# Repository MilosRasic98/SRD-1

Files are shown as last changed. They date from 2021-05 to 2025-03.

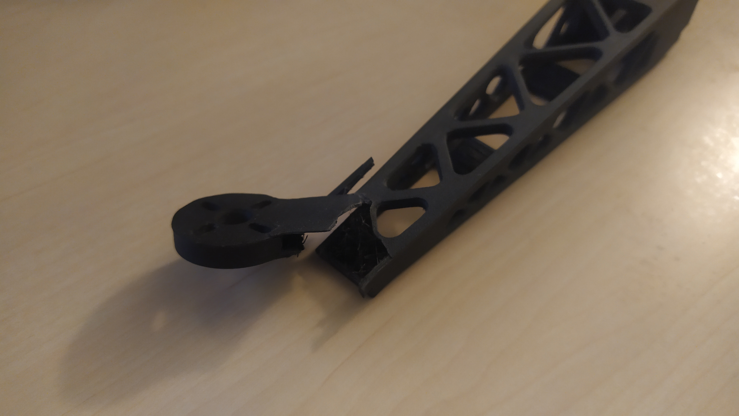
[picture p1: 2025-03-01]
Pictures/1621984355056.jpg

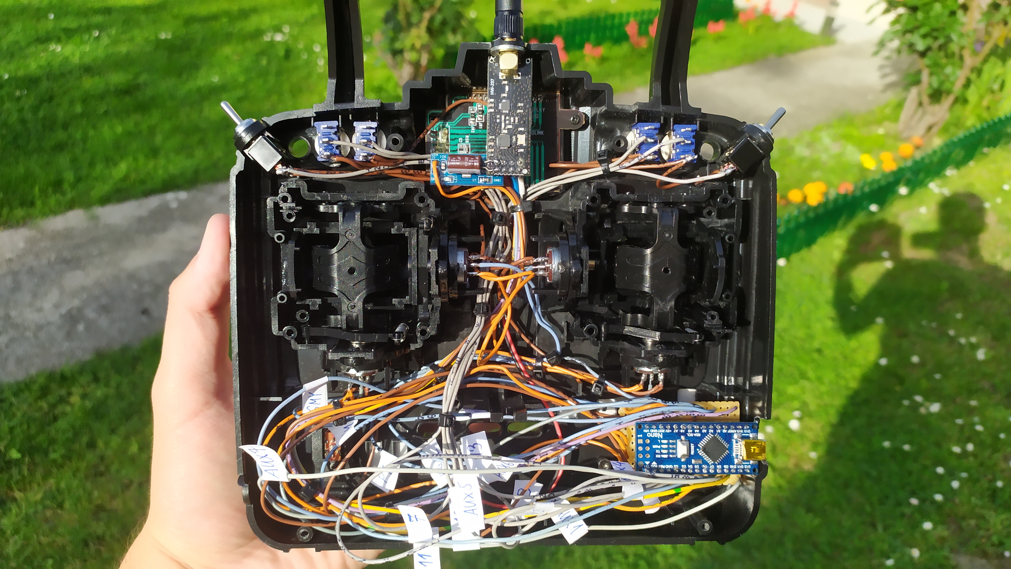
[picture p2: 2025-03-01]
Pictures/1621959381772.jpg

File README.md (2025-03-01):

# DIY Arduino Drone SRD-1

This repository covers the development of a completely open-source drone that I named the SRD-1. SRD-1 stands for Science & Research Drone 1 (the name was of course inspired by the legendary plane SR-71 Blackbird). For motors and ESCs, this drone uses the generic 2212 motors with the generic 30A ESC-s, meaning that those parts can be easily acquired by anyone. As for the rest of the electronics, all 3 major systems of the drone are based on individual Arduino Nanos. This includes:

1. Flight Controller - Arduino Nano, paired with an MPU6050, running the open-source MultiWii firmware
2. Radio Receiver - Arduino Nano, paired with the RF NRF module, code available in this repository
3. Radio Transmitter - Arduino Nano, paired with the RF NRF module, code available in this repository

If you check out the folders, you'll also be able to find all of the necessary CAD files for building your own drone. I will also be posting all of these models on Printables so you can download them there more easily if you would like. Links to Printables models:

1. https://www.printables.com/model/1212696-diy-arduino-drone-srd-1
2. https://www.printables.com/model/227060-raspberry-pi-hq-camera-drone-gimbal

I made this drone in 2021 as part of Element14 Communities, Attack of the Drones Project14 Competition, which this project managed to win! If you're interested in my write-up from back then, you can check this link here: https://community.element14.com/challenges-projects/project14/attackofthedrones/b/blog/posts/srd-1---3d-printed-drone-arduino-raspberry---june-11th-update---it-flies

Below, you can find some pictures of the finished drone, flight videos, and crash videos, of course!











My goal with this drone was to make it capable, but at the same time, make it as cheap as possible. This is why for the construction of the drone, I went with mostly 3D printed parts, as well as some easily obtainable hardware like PVC pipes so that anyone trying to replicate the drone can have the easiest time possible! Here are some flight videos of the drone, some successful, some a bit less successful, as you can see! Hope you like my sophisticated safety mechanism!

Flight 1

IMAGE ALT TEXT HERE (https://www.youtube.com/watch?v=f9ZAgGi6Brw)

Flight 2

IMAGE ALT TEXT HERE (https://www.youtube.com/watch?v=CNurr2BLMr8)

Flight 3

IMAGE ALT TEXT HERE (https://www.youtube.com/watch?v=EGkVoUZHSek)

Flight 4

IMAGE ALT TEXT HERE (https://www.youtube.com/watch?v=9p4l3mPER5Y)

Drone Crash

IMAGE ALT TEXT HERE (https://www.youtube.com/watch?v=lXBSGYBcmdE)

If you're considering making a similar drone and are curious about the lift capabilities, before making this drone, I made a drone motor test stand to find out what kind of thrust I was working with (you can check out the thrust stand, which is also an open-source project here: https://github.com/MilosRasic98/BLDC-Thrust-Tester), each motor could produce 870g of thrust. To get good performance out of the drone, ideally, you would like to keep it below 1.75kg, which is around half the weight of the maximum thrust with all 4 motors at full throttle.



My ultimate goal was to equip this drone with a Raspberry Pi and a Raspberry Pi Camera so I could do some recording and some more advanced stuff, but I never got around to the software part of it. However, I have done CAD models and printed out a gimbal for the Raspberry Pi HQ Camera module as well as some drone mounts for the Raspberry Pi 4. You can find the CAD files for each of these in the 3D Model directories or on the Printables links that I've linked at the beginning of this Readme file.





As mentioned above, both the RC transmitter and receiver were also made using Arduino Nano boards. To make my life a bit easier when I was making this drone, I used an RC transmitter body from an old RC helicopter I had and just connected it by soldering wires to the potentiometers. Another way you can go to recreate this would be using something like the Arduino joystick modules and keeping the code essentially the same.







I've tried my hardest to design all of the mechanical parts with the manufacturing process in mind, in this case, 3D printing. This is why I tried my best to minimize the support material used, as well as optimize the printability of the parts so that the parts can get the most strength where they need it. I've left a lot of comments in the technical drawings section, which you can check below, or check all of it in the technical drawings directory!





















These are the same principles I tried to keep when I designed the gimbal for the Raspberry Pi HQ Camera using the popular SG90 servo motors. Here, I used some pieces of rubber tubing to act as shock absorbers to at least try and remove some of the noise coming from the propellers while the drone is flying.



















Hope you like the project and that it at least inspires you to make something similar. Feel free to write to me if you have any questions with the project itself!

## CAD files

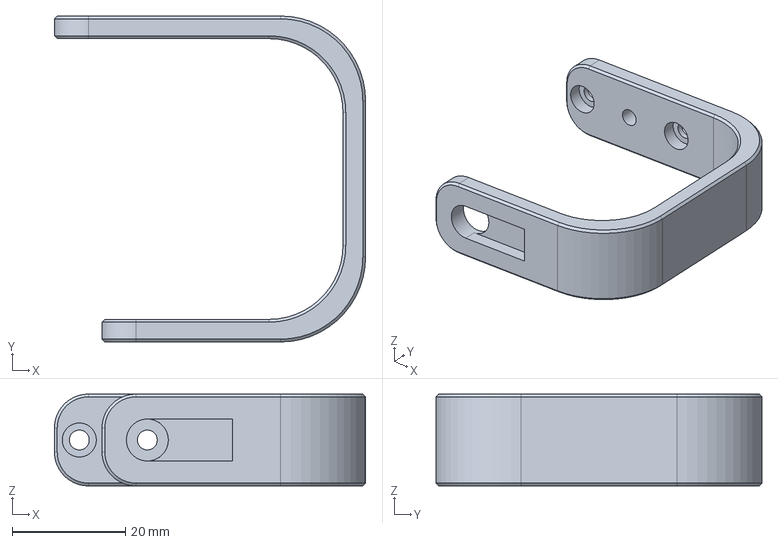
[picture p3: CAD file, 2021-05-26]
3D Models/SG90 Gimbal Assembly/Gimbal Main Arm.step
54.9 x 57.5 x 16.2 mm

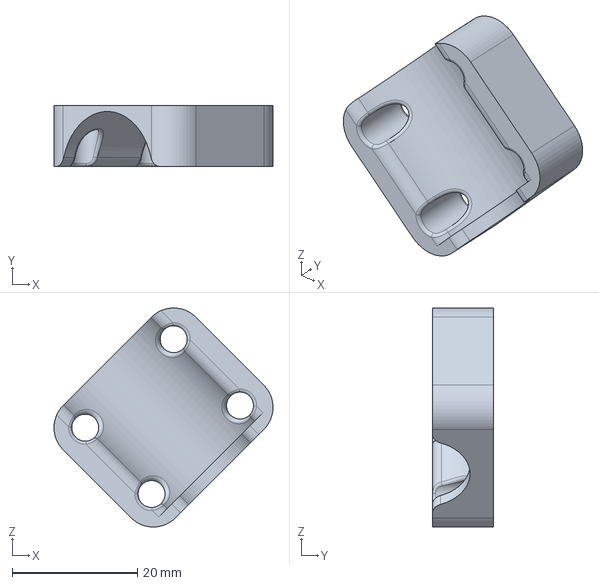
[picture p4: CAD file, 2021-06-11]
3D Models for the 20mm pipe version/Base Assembly/Pipe Arm Mount Half.step
35.0 x 9.75 x 35.0 mm

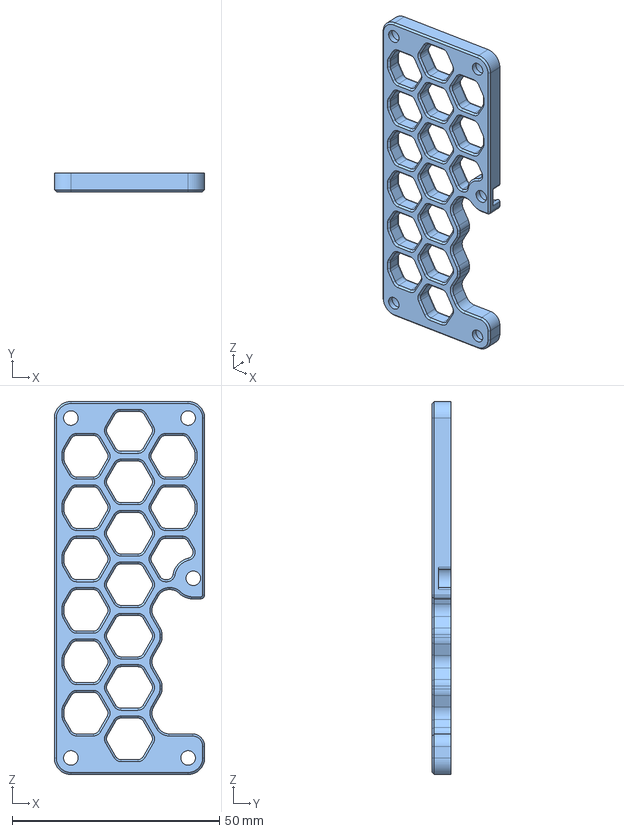
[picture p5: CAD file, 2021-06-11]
3D Models for the 20mm pipe version/Controller Assembly/Electronics Cover.step
36.3 x 4.50 x 90.0 mm

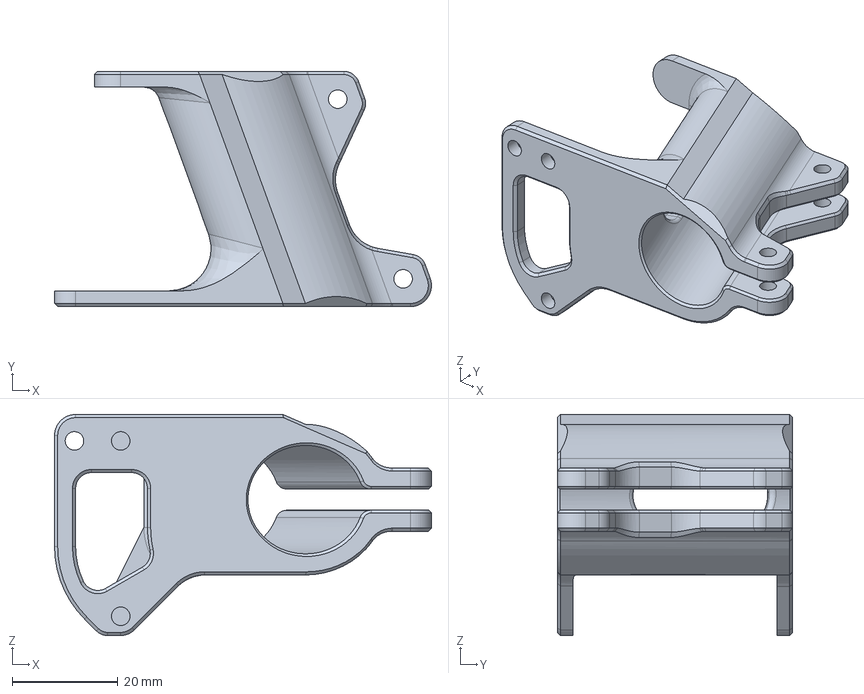
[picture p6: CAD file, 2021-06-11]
3D Models for the 20mm pipe version/Leg Assembly/Leg Holder.step
71.3 x 44.5 x 41.8 mm

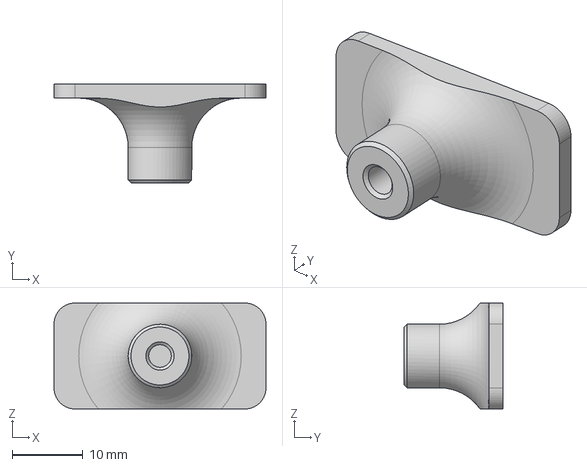
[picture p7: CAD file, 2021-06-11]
3D Models for the 20mm pipe version/Motor Alignment Tool/LevelMount.step
30.0 x 14.0 x 15.0 mm

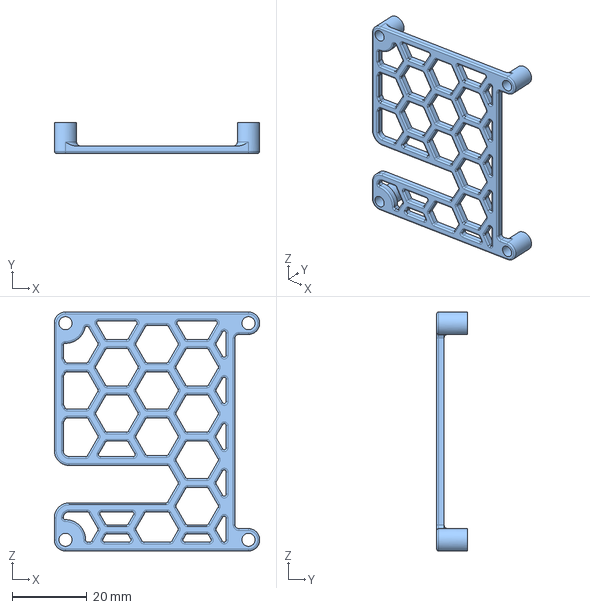
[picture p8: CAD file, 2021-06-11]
3D Models for the 20mm pipe version/Raspberry Pi Assembly/Raspberry Pi Cover.step
55.0 x 8.20 x 64.0 mm

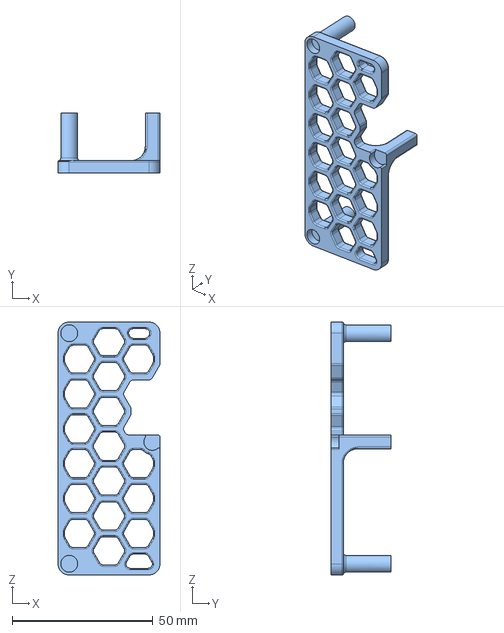
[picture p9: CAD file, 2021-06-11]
3D Models for the 20mm pipe version/Receiver Assembly/Receiver Cover.step
36.3 x 21.5 x 90.0 mm

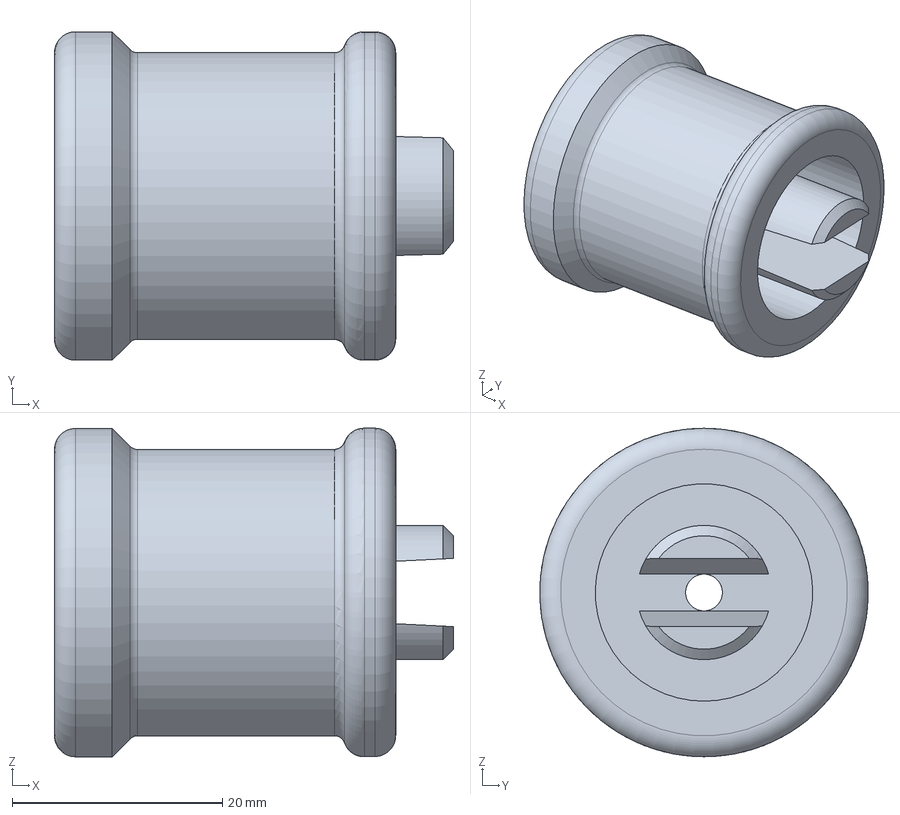
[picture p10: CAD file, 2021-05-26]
3D Models/Base Assembly/Foot.step
38.0 x 31.3 x 31.3 mm

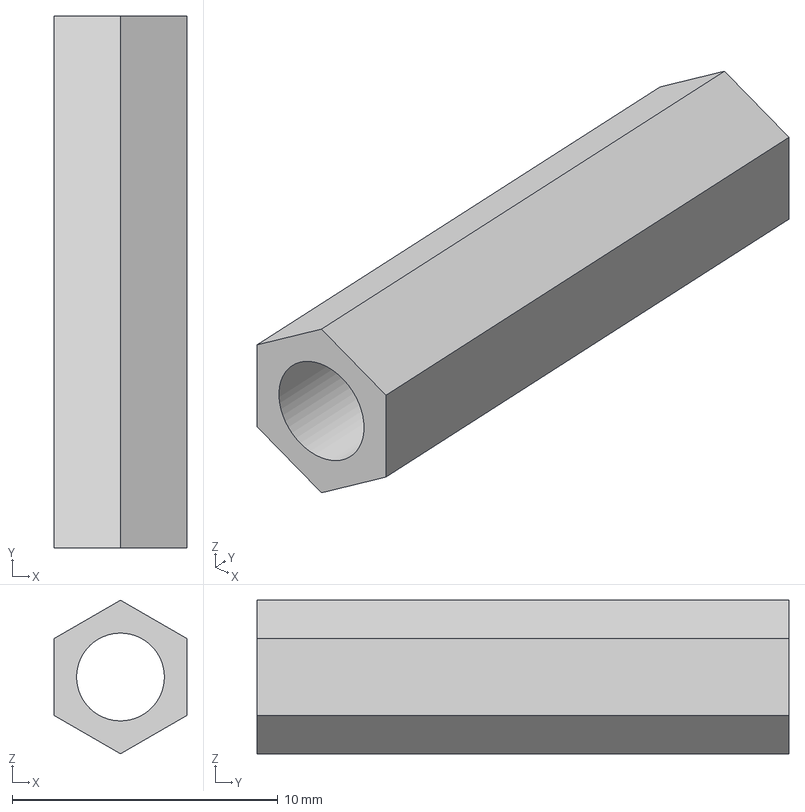
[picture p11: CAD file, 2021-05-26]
3D Models/Electronics Assembly/StandOff.step
5.00 x 20.0 x 5.77 mm

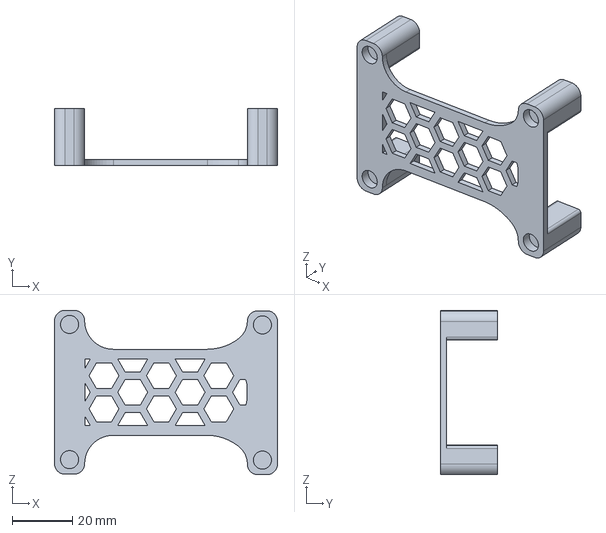
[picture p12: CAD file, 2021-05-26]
3D Models/Power Assembly/Cover.step
74.0 x 19.0 x 54.6 mm

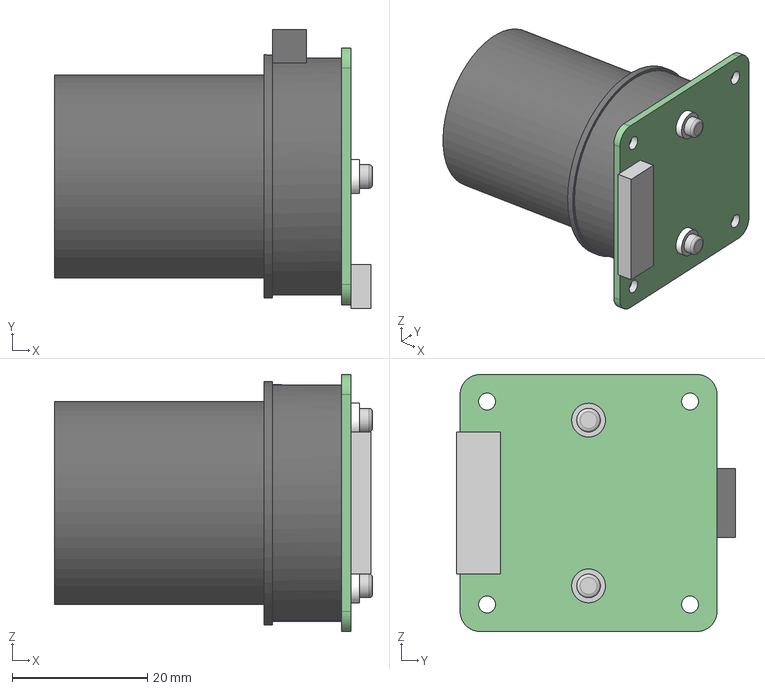
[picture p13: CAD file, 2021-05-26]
3D Models/SG90 Gimbal Assembly/Raspberry HQ Camera.step
47.0 x 41.2 x 38.0 mm

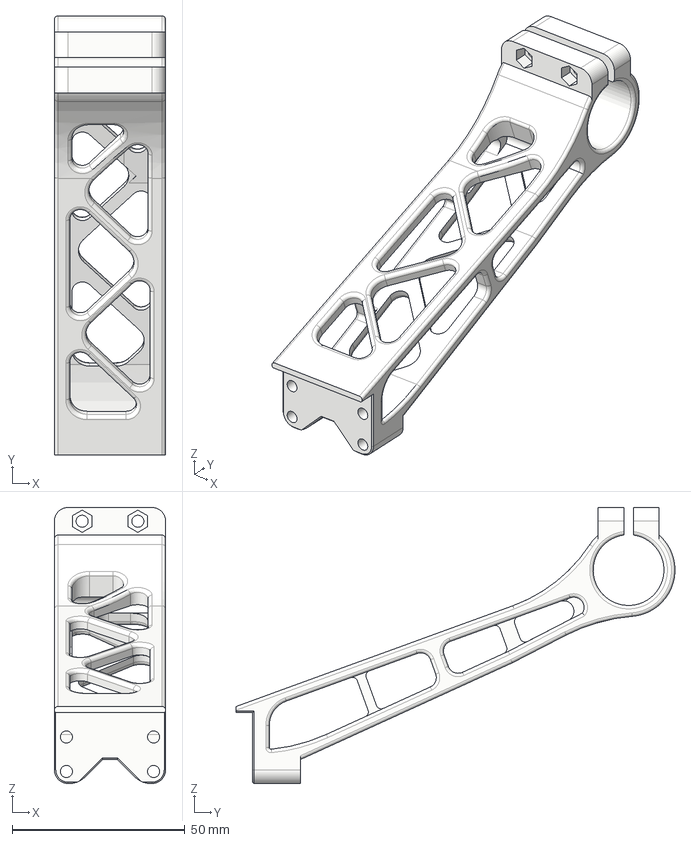
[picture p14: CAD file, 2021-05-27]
3D Models/Wooden Base Version/Left Leg.step
32.3 x 127.2 x 80.0 mm

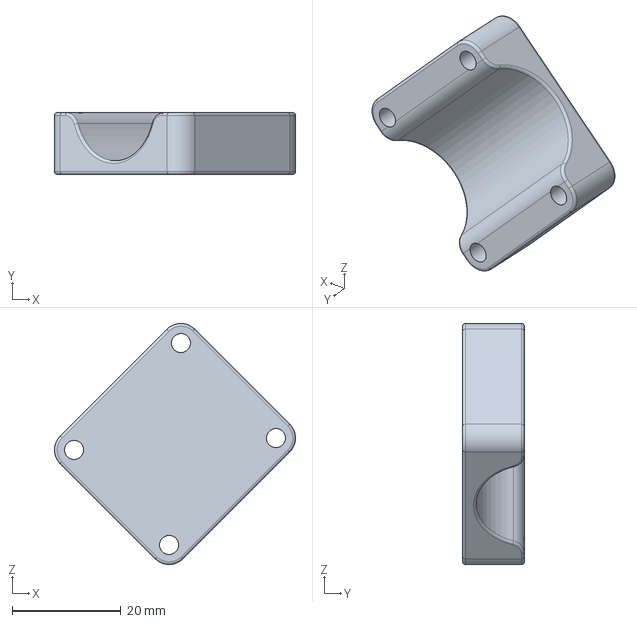
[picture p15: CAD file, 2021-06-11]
3D Models for the 20mm pipe version/Base Assembly/Motor Mount.step
44.3 x 11.4 x 44.3 mm

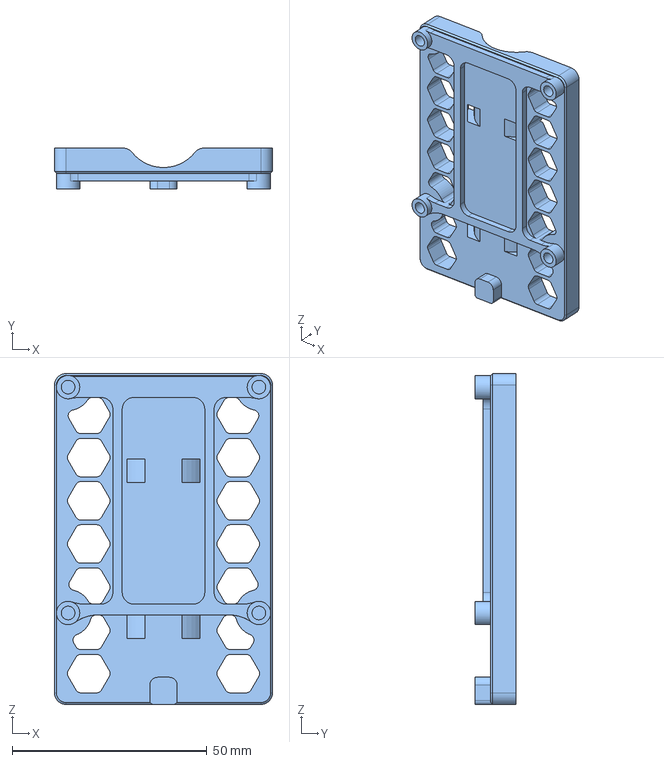
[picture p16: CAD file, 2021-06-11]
3D Models for the 20mm pipe version/Raspberry Pi Assembly/Raspberry Pi Mount.step
56.0 x 10.5 x 85.0 mm

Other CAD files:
3D Models for the 20mm pipe version/Receiver Assembly/Receiver Mount.step
3D Models/Base Assembly/Drone Arm.step
3D Models/Electronics Assembly/Board.step
3D Models/Power Assembly/3S LiPo .step
3D Models for the 20mm pipe version/Base Assembly/Motor Mount.stl
3D Models for the 20mm pipe version/Base Assembly/Motor Plate.step
3D Models for the 20mm pipe version/Base Assembly/Motor Plate.stl
3D Models for the 20mm pipe version/Base Assembly/Pipe Arm Mount Half.stl
3D Models for the 20mm pipe version/Controller Assembly/Electronics Cover.stl
3D Models for the 20mm pipe version/Leg Assembly/Leg Cover.step
3D Models for the 20mm pipe version/Leg Assembly/Leg Cover.stl
3D Models for the 20mm pipe version/Leg Assembly/Leg Holder.stl
3D Models for the 20mm pipe version/Leg Assembly/Leg Locker.step
3D Models for the 20mm pipe version/Leg Assembly/Leg Locker.stl
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

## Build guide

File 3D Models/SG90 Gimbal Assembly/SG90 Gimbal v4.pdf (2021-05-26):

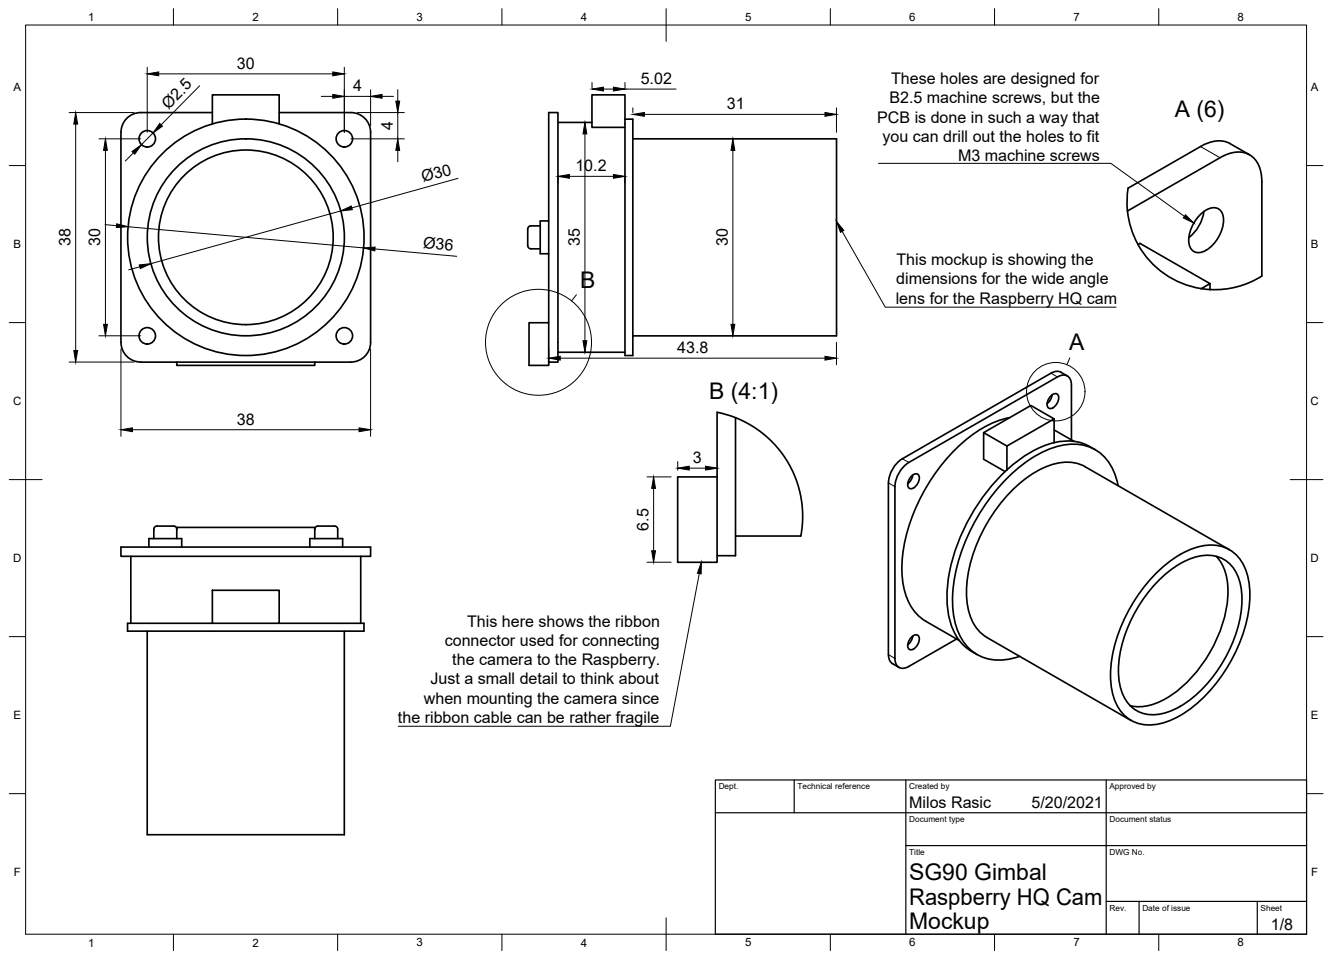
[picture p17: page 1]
Title; DWG No.; Rev.; Date of issue; Sheet; M3 machine screws

These holes are designed for
B2.5 machine screws, but the
PCB is done in such a way that
you can drill out the holes to fit

This mockup is showing the
dimensions for the wide angle
lens for the Raspberry HQ cam

This here shows the ribbon
connector used for connecting
the camera to the Raspberry.
Just a small detail to think about
when mounting the camera since
the ribbon cable can be rather fragile

Dept. | Technical reference | Created by Milos Rasic 5/20/2021 | Approved by

Document type | Document status

SG90 Gimbal
Raspberry HQ Cam
Mockup

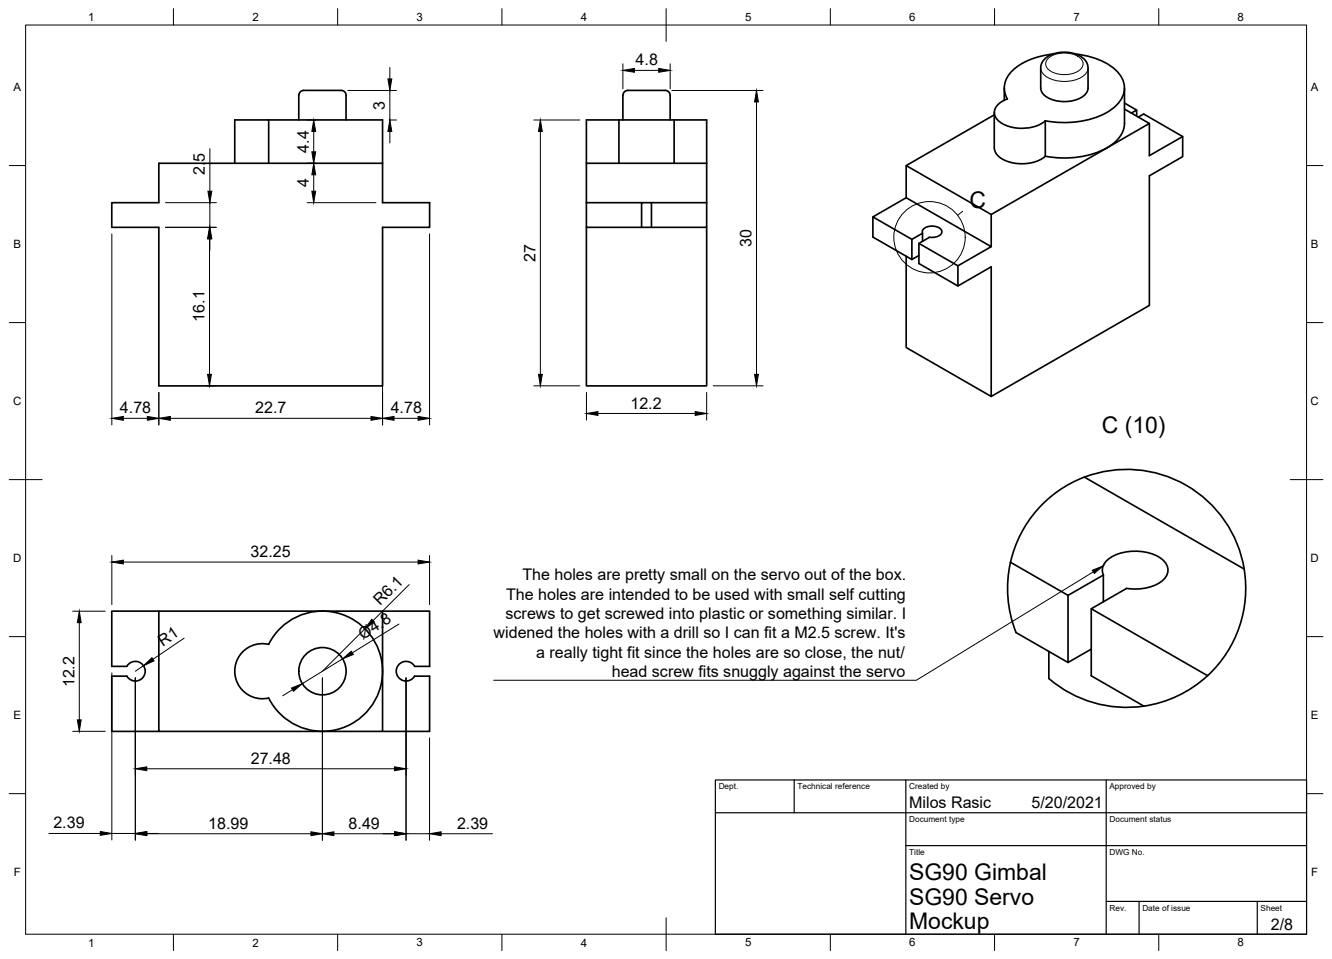
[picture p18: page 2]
Title; DWG No.; SG90 Servo; SG90 Gimbal

The holes are pretty small on the servo out of the box.
The holes are intended to be used with small self cutting
screws to get screwed into plastic or something similar. I
widened the holes with a drill so I can fit a M2.5 screw. It's
a really tight fit since the holes are so close, the nut/

head screw fits snuggly against the servo

Dept. | Technical reference | Created by Milos Rasic 5/20/2021 | Approved by

Document type | Document status

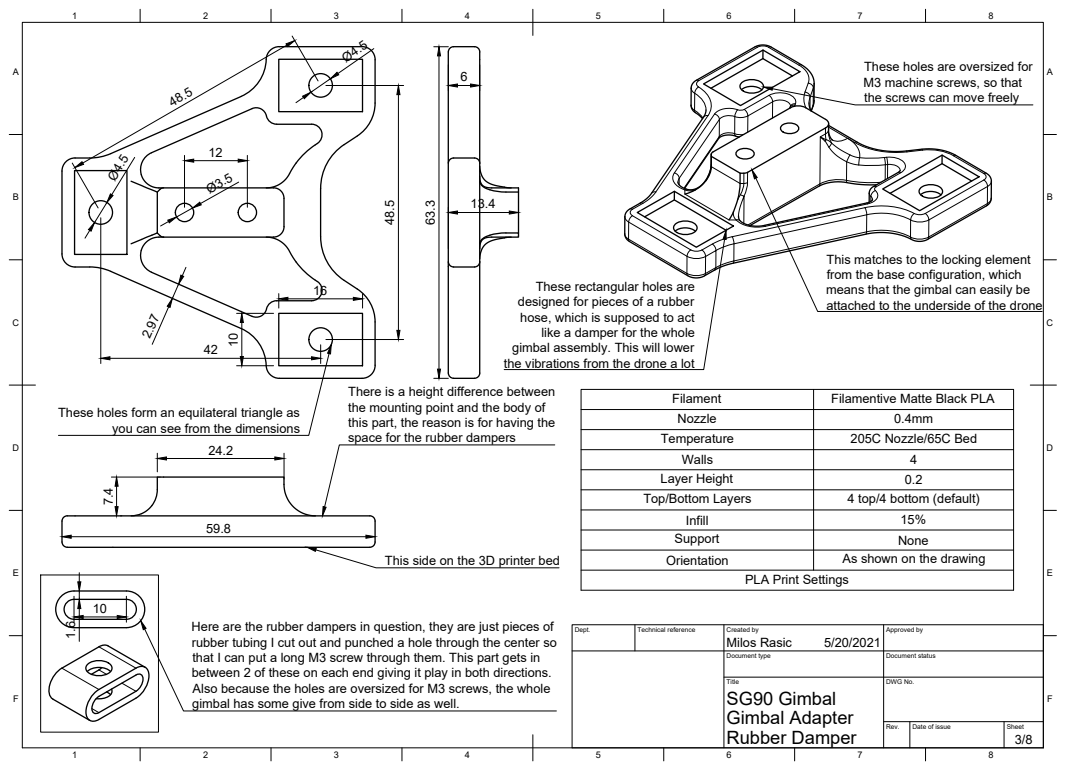
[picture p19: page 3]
Title; DWG No.; Rubber Damper; Gimbal Adapter; SG90 Gimbal

These holes are oversized for
M3 machine screws, so that
the screws can move freely

This matches to the locking element
from the base configuration, which
means that the gimbal can easily be
attached to the underside of the drone

These rectangular holes are
designed for pieces of a rubber
hose, which is supposed to act
like a damper for the whole
gimbal assembly. This will lower
the vibrations from the drone a lot

There is a height difference between
the mounting point and the body of
this part, the reason is for having the

Filament | Filamentive Matte Black PLA
Nozzle | 0.4mm
Temperature | 205C Nozzle/65C Bed
Walls | 4
Layer Height | 0.2
Top/Bottom Layers | 4 top/4 bottom (default)

These holes form an equilateral triangle as

you can see from the dimensions

space for the rubber dampers 1.6

Infill | 15%
Support | None
Orientation | As shown on the drawing

This side on the 3D printer bed

PLA Print Settings

Here are the rubber dampers in question, they are just pieces of
rubber tubing I cut out and punched a hole through the center so
that I can put a long M3 screw through them. This part gets in
between 2 of these on each end giving it play in both directions.
Also because the holes are oversized for M3 screws, the whole
gimbal has some give from side to side as well.

Dept. | Technical reference | Created by Milos Rasic 5/20/2021 | Approved by

Document type | Document status

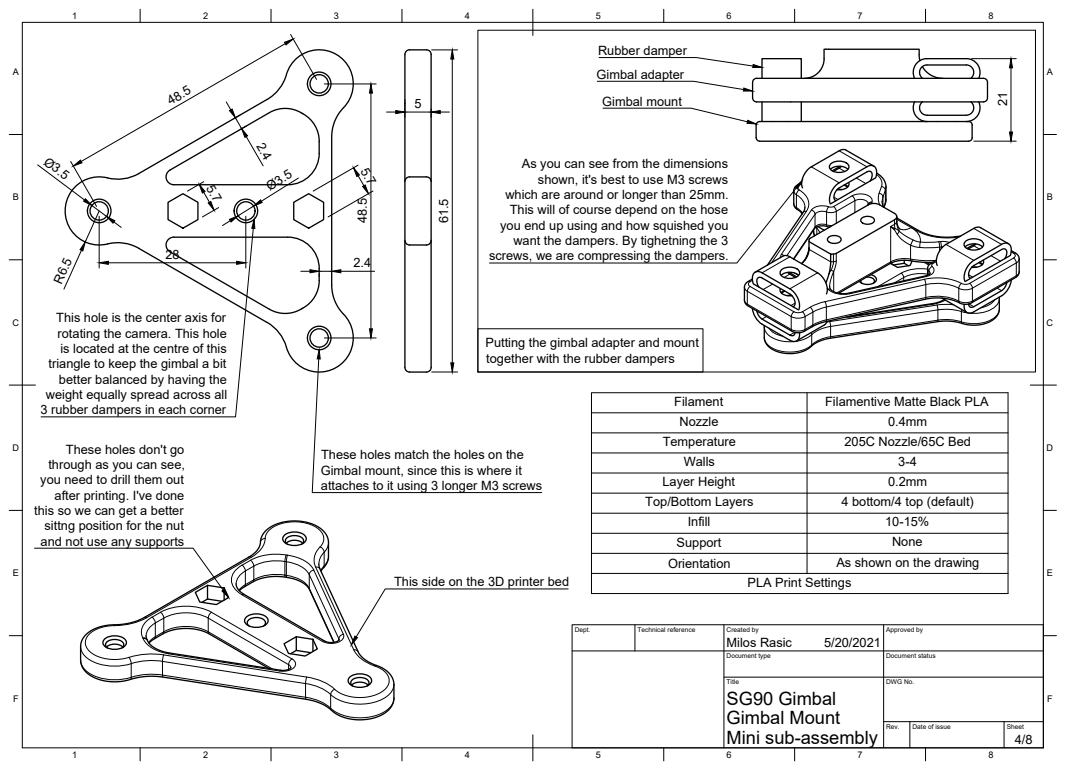
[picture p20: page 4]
Title; DWG No.; Rubber damper; Gimbal adapter; Gimbal mount

As you can see from the dimensions
shown, it's best to use M3 screws
which are around or longer than 25mm.
This will of course depend on the hose
you end up using and how squished you
want the dampers. By tighetning the 3
screws, we are compressing the dampers.

This hole is the center axis for
rotating the camera. This hole
is located at the centre of this
triangle to keep the gimbal a bit
better balanced by having the
weight equally spread across all
3 rubber dampers in each corner

Putting the gimbal adapter and mount
together with the rubber dampers

Filament | Filamentive Matte Black PLA
Nozzle | 0.4mm
Temperature | 205C Nozzle/65C Bed
Walls | 3-4
Layer Height | 0.2mm
Top/Bottom Layers | 4 bottom/4 top (default)

These holes don't go
through as you can see,
you need to drill them out
after printing. I've done
this so we can get a better
sittng position for the nut
and not use any supports

These holes match the holes on the
Gimbal mount, since this is where it
attaches to it using 3 longer M3 screws

Infill | 10-15%
Support | None
Orientation | As shown on the drawing

This side on the 3D printer bed

PLA Print Settings

Dept. | Technical reference | Created by Milos Rasic 5/20/2021 | Approved by

Document type | Document status

SG90 Gimbal
Gimbal Mount
Mini sub-assembly

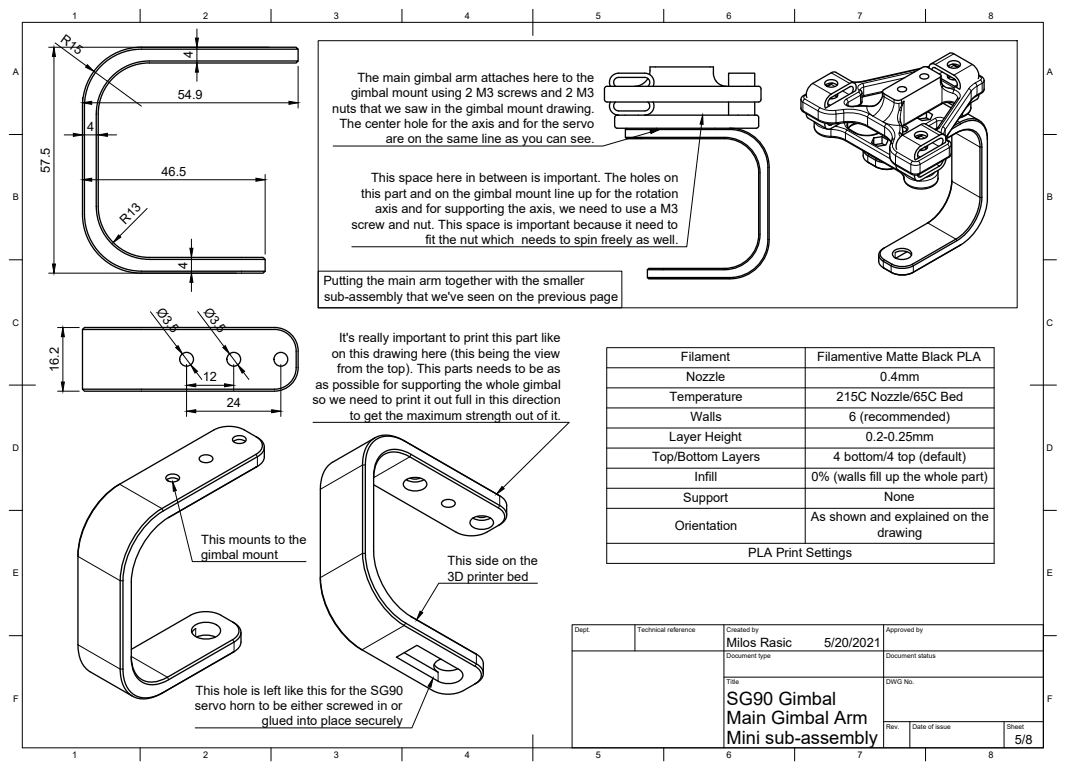
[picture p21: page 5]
Title; DWG No.; gimbal mount; This side on the; 3D printer bed

The main gimbal arm attaches here to the
gimbal mount using 2 M3 screws and 2 M3
nuts that we saw in the gimbal mount drawing.
The center hole for the axis and for the servo

are on the same line as you can see.

This space here in between is important. The holes on
this part and on the gimbal mount line up for the rotation
axis and for supporting the axis, we need to use a M3
screw and nut. This space is important because it need to

fit the nut which needs to spin freely as well.

Putting the main arm together with the smaller
sub-assembly that we've seen on the previous page

It's really important to print this part like
on this drawing here (this being the view
from the top). This parts needs to be as
as possible for supporting the whole gimbal
so we need to print it out full in this direction

Filament | Filamentive Matte Black PLA
Nozzle | 0.4mm
Temperature | 215C Nozzle/65C Bed
Walls | 6 (recommended)
Layer Height | 0.2-0.25mm
Top/Bottom Layers | 4 bottom/4 top (default)

to get the maximum strength out of it.

Infill | 0% (walls fill up the whole part)
Support | None
Orientation | As shown and explained on the drawing

This mounts to the

PLA Print Settings

Dept. | Technical reference | Created by Milos Rasic 5/20/2021 | Approved by

Document type | Document status

SG90 Gimbal
Main Gimbal Arm
Mini sub-assembly

This hole is left like this for the SG90
servo horn to be either screwed in or

glued into place securely

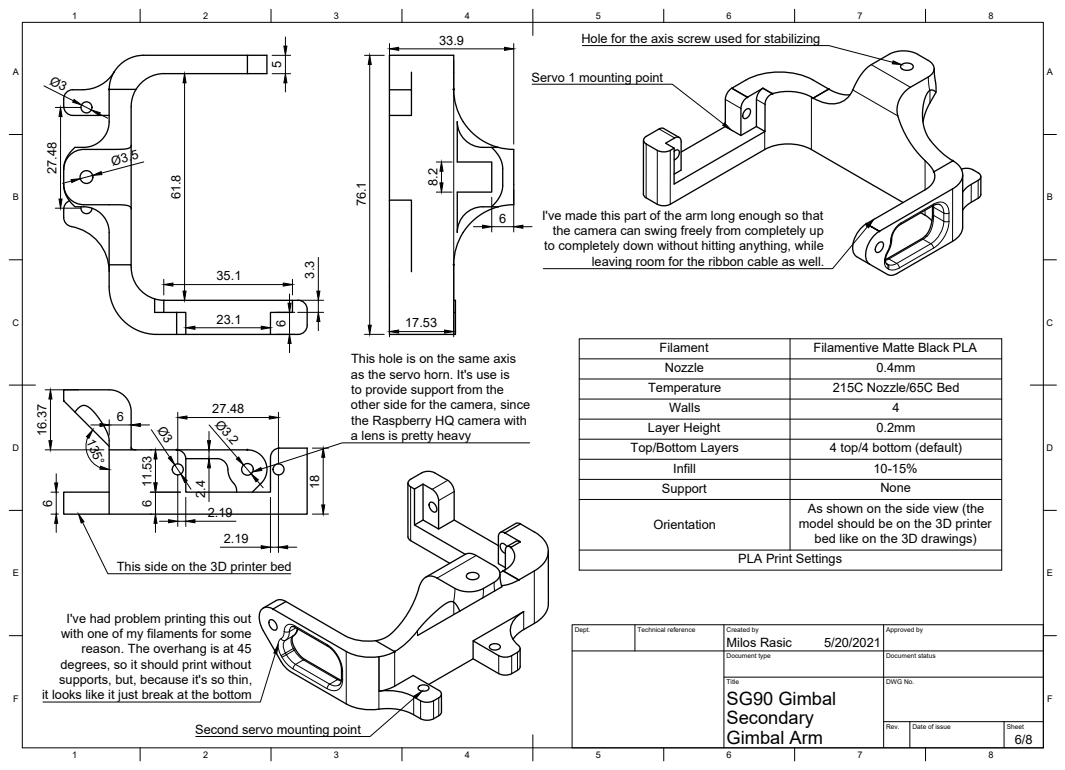
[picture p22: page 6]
Title; DWG No.; Gimbal Arm; SG90 Gimbal; a lens is pretty heavy Ø3; This side on the 3D printer bed; PLA Print Settings

Hole for the axis screw used for stabilizing

Servo 1 mounting point

I've made this part of the arm long enough so that
the camera can swing freely from completely up
to completely down without hitting anything, while

leaving room for the ribbon cable as well.

Filament | Filamentive Matte Black PLA
Nozzle | 0.4mm
Temperature | 215C Nozzle/65C Bed
Walls | 4
Layer Height | 0.2mm
Top/Bottom Layers | 4 top/4 bottom (default)

This hole is on the same axis
as the servo horn. It's use is
to provide support from the
other side for the camera, since
the Raspberry HQ camera with

Infill | 10-15%
Support | None
Orientation | As shown on the side view (the model should be on the 3D printer bed like on the 3D drawings)

I've had problem printing this out
with one of my filaments for some
reason. The overhang is at 45
degrees, so it should print without
supports, but, because it's so thin,
it looks like it just break at the bottom

Dept. | Technical reference | Created by Milos Rasic 5/20/2021 | Approved by

Document type | Document status

Second servo mounting point

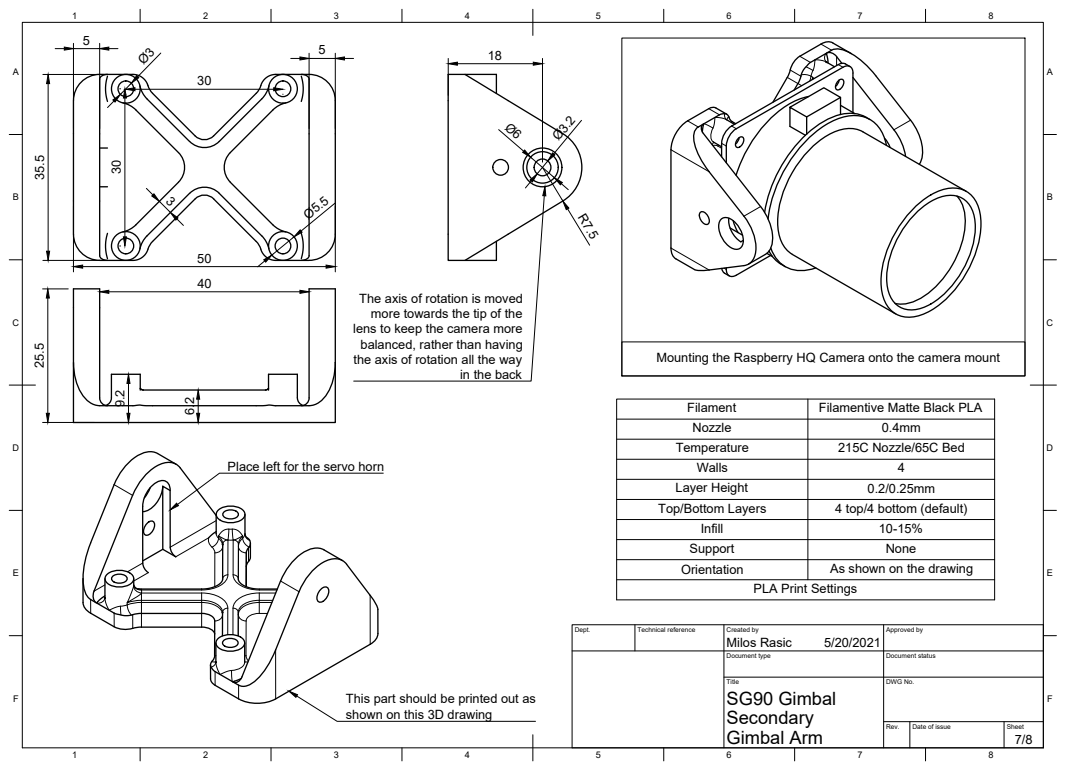
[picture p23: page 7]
Title; DWG No.; Gimbal Arm; SG90 Gimbal

The axis of rotation is moved
more towards the tip of the
lens to keep the camera more
balanced, rather than having
the axis of rotation all the way

Mounting the Raspberry HQ Camera onto the camera mount

in the back

Filament | Filamentive Matte Black PLA
Nozzle | 0.4mm
Temperature | 215C Nozzle/65C Bed
Walls | 4
Layer Height | 0.2/0.25mm
Top/Bottom Layers | 4 top/4 bottom (default)

Place left for the servo horn

Infill | 10-15%
Support | None
Orientation | As shown on the drawing

PLA Print Settings

Dept. | Technical reference | Created by Milos Rasic 5/20/2021 | Approved by

Document type | Document status

This part should be printed out as
shown on this 3D drawing

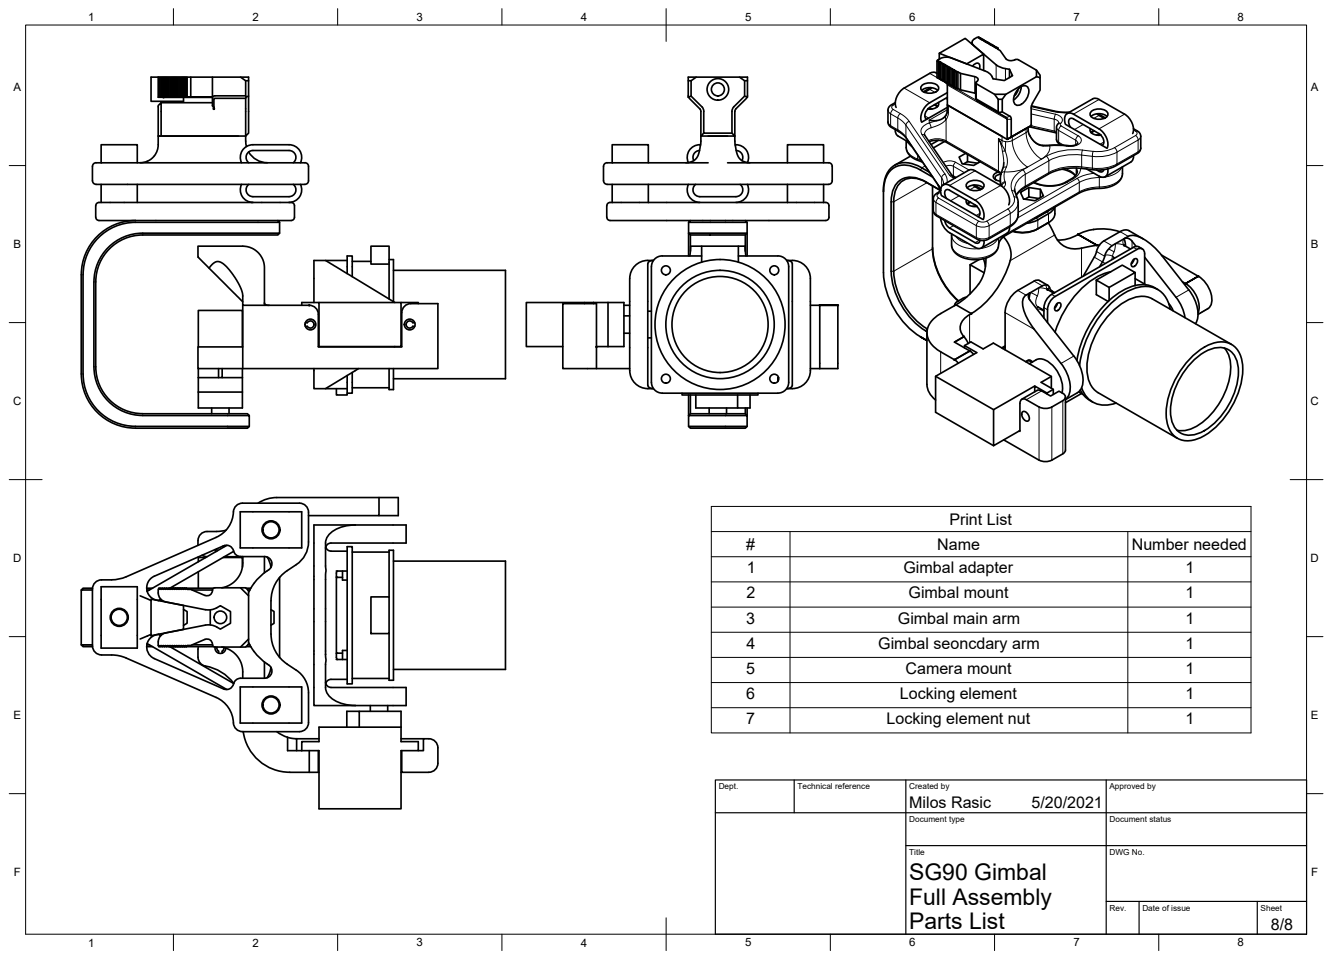
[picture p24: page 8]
Title; DWG No.; Parts List; Full Assembly; SG90 Gimbal; Print List

# | Name | Number needed
1 | Gimbal adapter | 1
2 | Gimbal mount | 1
3 | Gimbal main arm | 1
4 | Gimbal seoncdary arm | 1
5 | Camera mount | 1
6 | Locking element | 1
7 | Locking element nut | 1

Dept. | Technical reference | Created by Milos Rasic 5/20/2021 | Approved by

Document type | Document status

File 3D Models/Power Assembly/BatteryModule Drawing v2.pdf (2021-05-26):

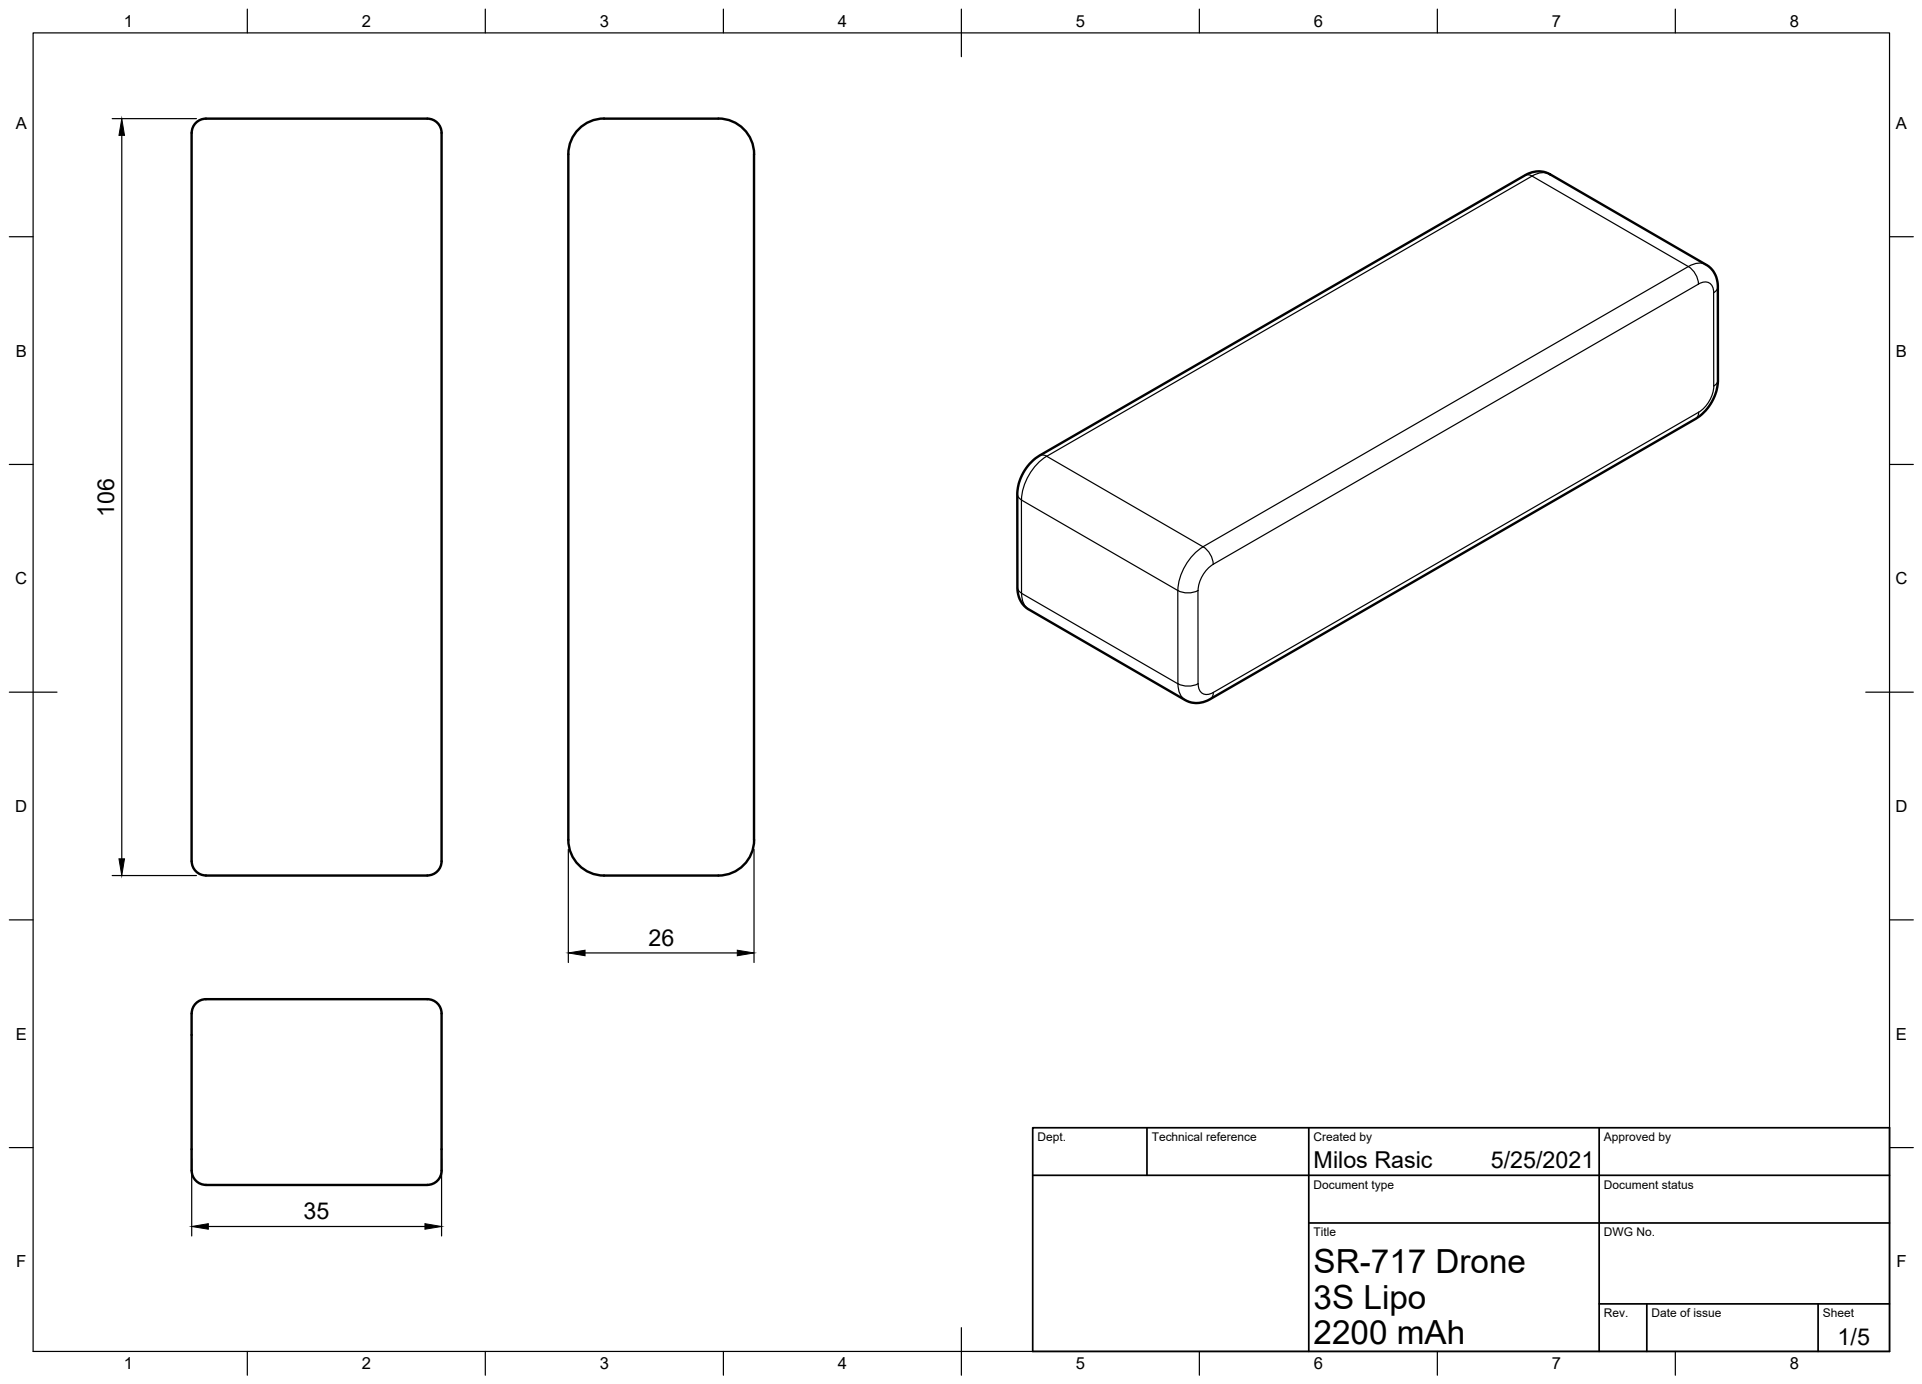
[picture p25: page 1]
Title; DWG No.; Rev.; Date of issue; Sheet; 2200 mAh; 3S Lipo; SR-717 Drone; Milos Rasic 106

Dept. | Technical reference | Created by 5/25/2021 | Approved by

Document type | Document status

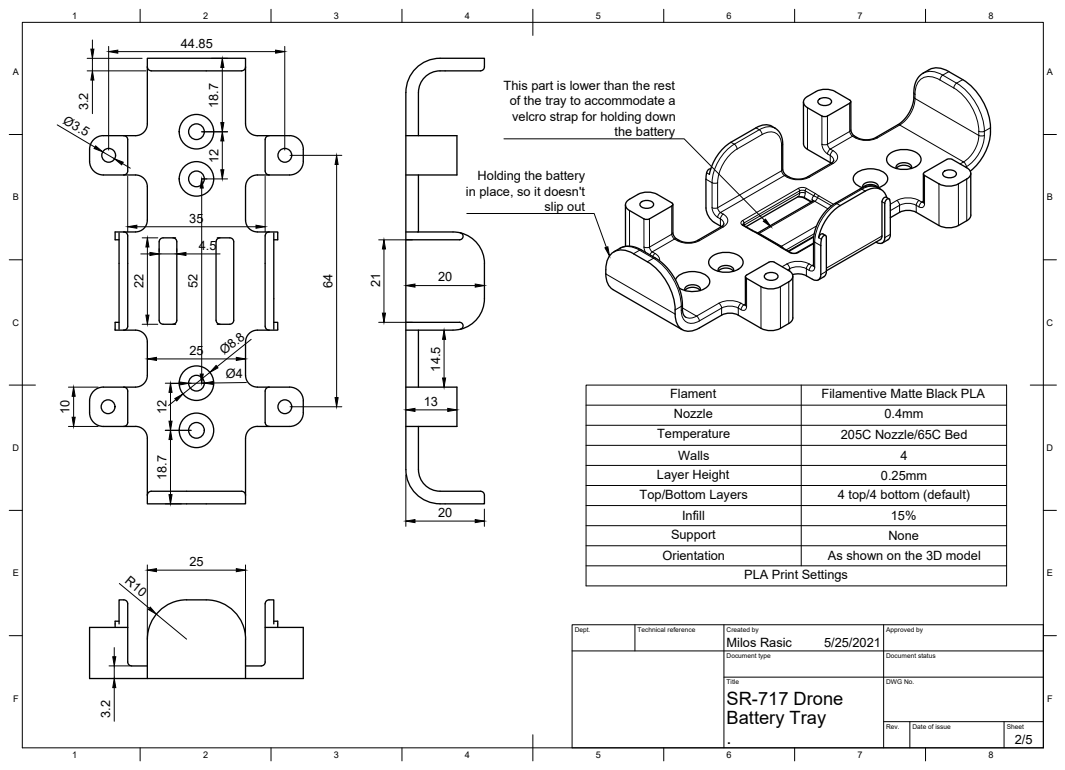
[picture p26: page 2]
Title; DWG No.; Rev.; Date of issue; Sheet .; Battery Tray; SR-717 Drone; the battery; slip out

This part is lower than the rest
of the tray to accommodate a
velcro strap for holding down

Holding the battery
in place, so it doesn't

Flament | Filamentive Matte Black PLA
Nozzle | 0.4mm
Temperature | 205C Nozzle/65C Bed
Walls | 4
Layer Height | 0.25mm
Top/Bottom Layers | 4 top/4 bottom (default)

Infill | 15%
Support | None
Orientation | As shown on the 3D model

R10 PLA Print Settings

Dept. | Technical reference | Created by Milos Rasic 5/25/2021 | Approved by

Document type | Document status

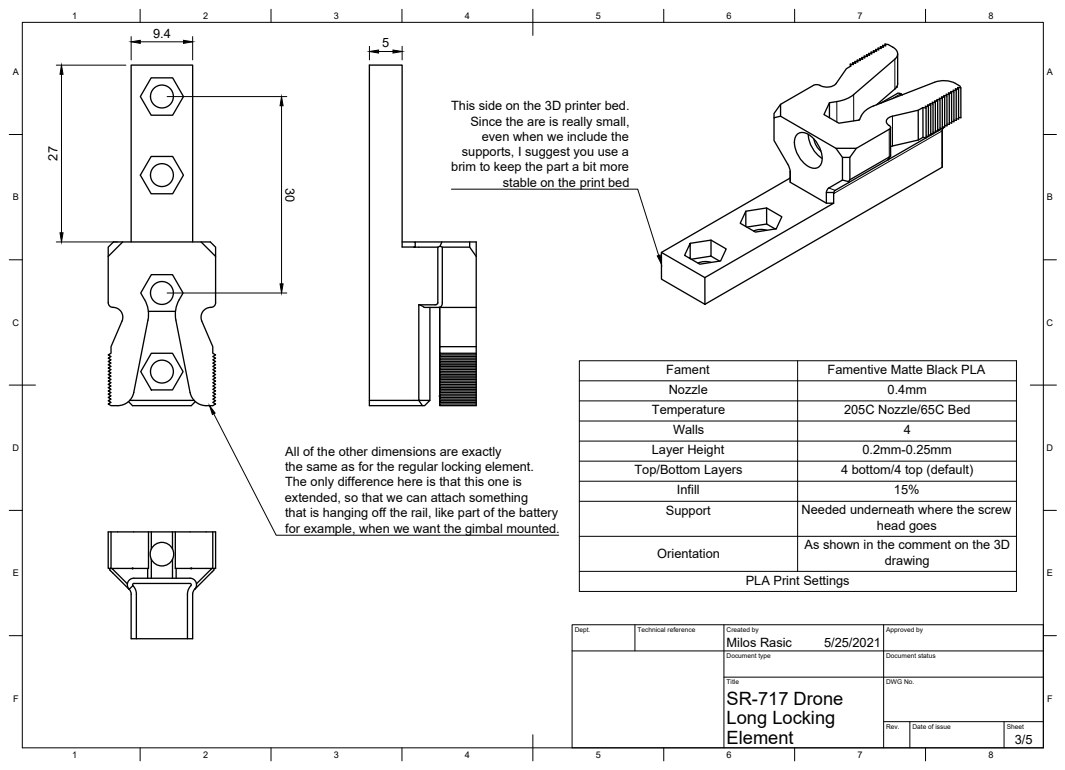
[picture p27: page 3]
Title; DWG No.; Long Locking; SR-717 Drone; Milos Rasic 27

This side on the 3D printer bed.
Since the are is really small,
even when we include the
supports, I suggest you use a
brim to keep the part a bit more

stable on the print bed

Fament | Famentive Matte Black PLA
Nozzle | 0.4mm
Temperature | 205C Nozzle/65C Bed
Walls | 4
Layer Height | 0.2mm-0.25mm
Top/Bottom Layers | 4 bottom/4 top (default)

All of the other dimensions are exactly
the same as for the regular locking element.
The only difference here is that this one is
extended, so that we can attach something
that is hanging off the rail, like part of the battery
for example, when we want the gimbal mounted.

Infill | 15%
Support | Needed underneath where the screw head goes

Orientation | As shown in the comment on the 3D drawing

PLA Print Settings

Dept. | Technical reference | Created by 5/25/2021 | Approved by

Document type | Document status

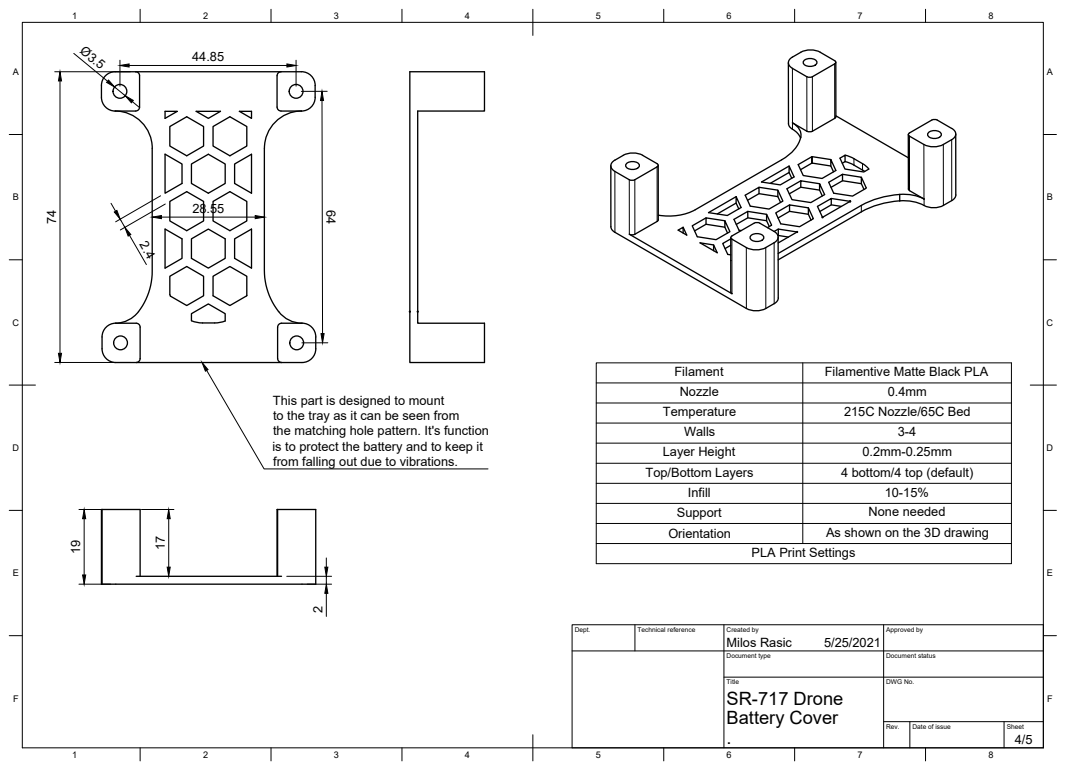
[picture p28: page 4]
Title; DWG No.; Rev.; Date of issue; Sheet .; Battery Cover; SR-717 Drone

Filament | Filamentive Matte Black PLA
Nozzle | 0.4mm
Temperature | 215C Nozzle/65C Bed
Walls | 3-4
Layer Height | 0.2mm-0.25mm
Top/Bottom Layers | 4 bottom/4 top (default)

This part is designed to mount
to the tray as it can be seen from
the matching hole pattern. It's function
is to protect the battery and to keep it
from falling out due to vibrations.

Infill | 10-15%
Support | None needed
Orientation | As shown on the 3D drawing

PLA Print Settings

Dept. | Technical reference | Created by Milos Rasic 5/25/2021 | Approved by

Document type | Document status

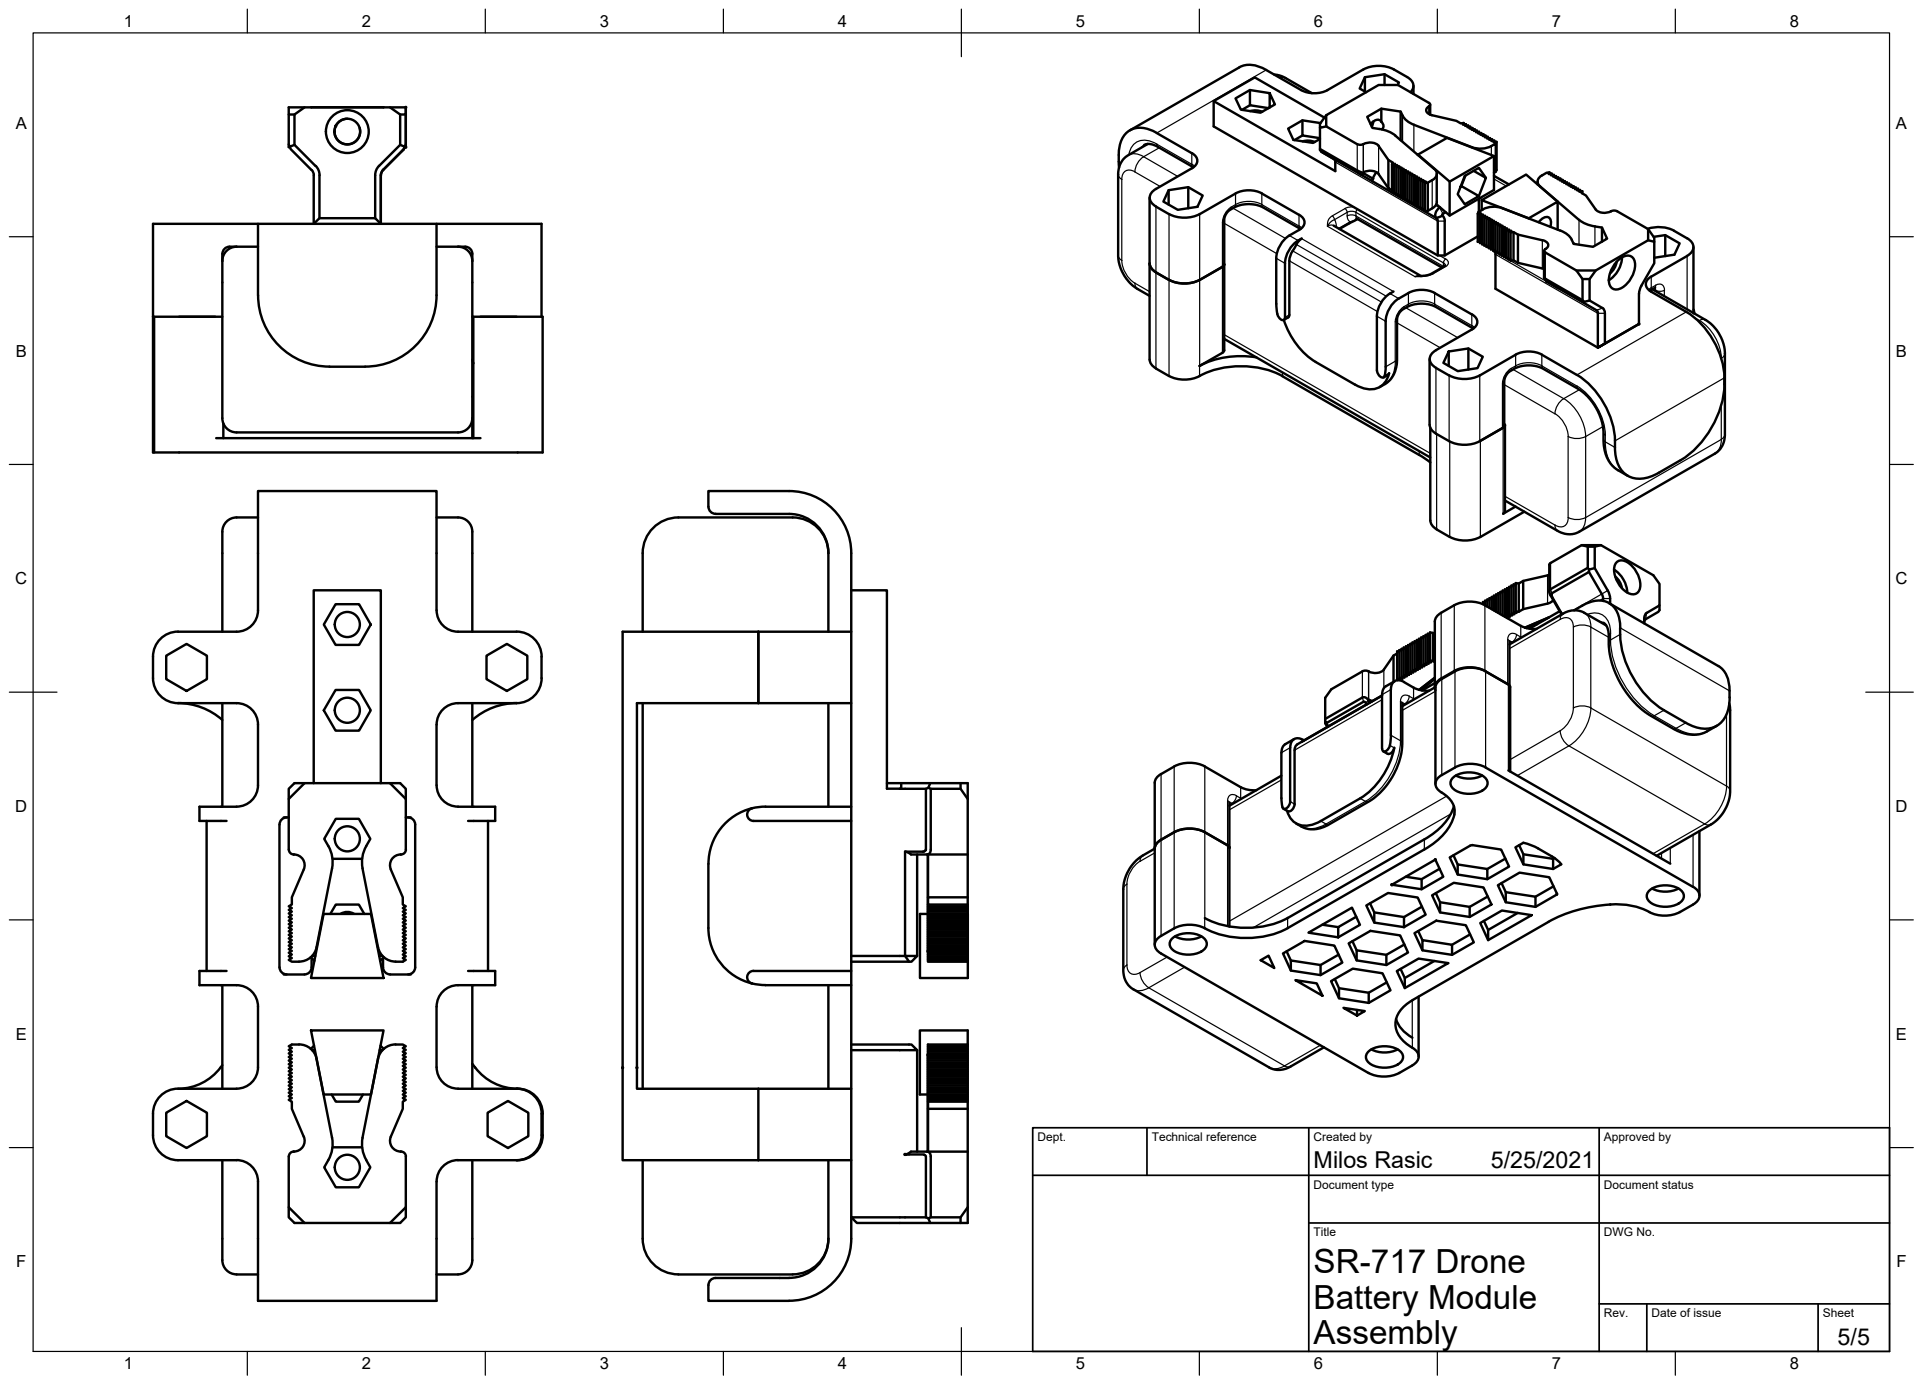
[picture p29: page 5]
Title; DWG No.; Battery Module; SR-717 Drone

Dept. | Technical reference | Created by Milos Rasic 5/25/2021 | Approved by

Document type | Document status

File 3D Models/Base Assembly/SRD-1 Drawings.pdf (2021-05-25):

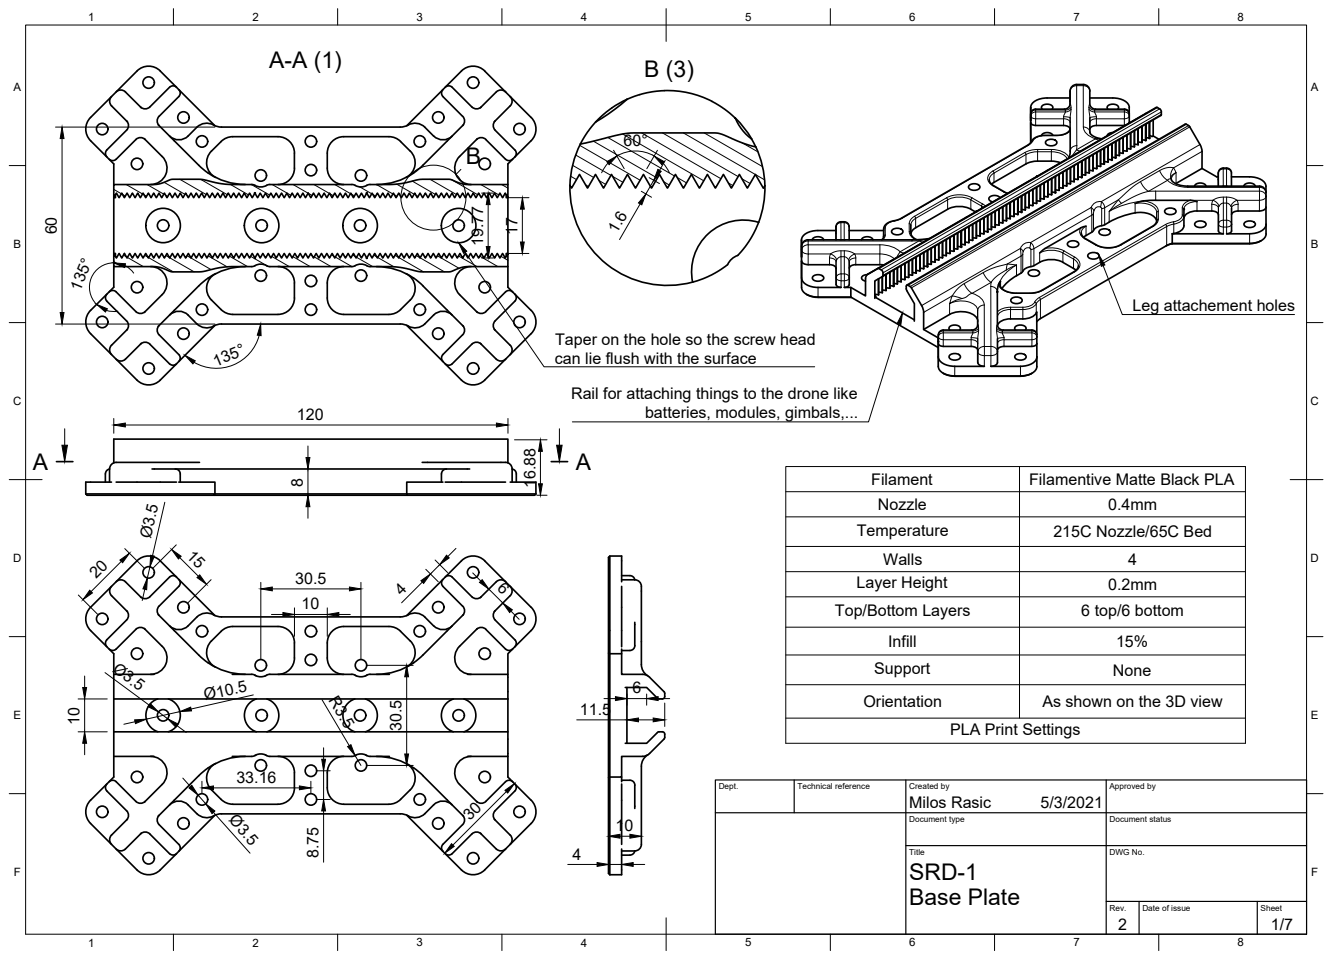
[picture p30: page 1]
Title; DWG No.; Rev.; Date of issue; Sheet; Base Plate

Leg attachement holes

Taper on the hole so the screw head
can lie flush with the surface

Rail for attaching things to the drone like

batteries, modules, gimbals,...

Filament | Filamentive Matte Black PLA
Nozzle | 0.4mm
Temperature | 215C Nozzle/65C Bed

Walls | 4
Layer Height | 0.2mm
Top/Bottom Layers | 6 top/6 bottom

Infill | 15%
Support | None

Orientation | As shown on the 3D view

PLA Print Settings

Dept. | Technical reference | Created by Milos Rasic 5/3/2021 | Approved by

Document type | Document status

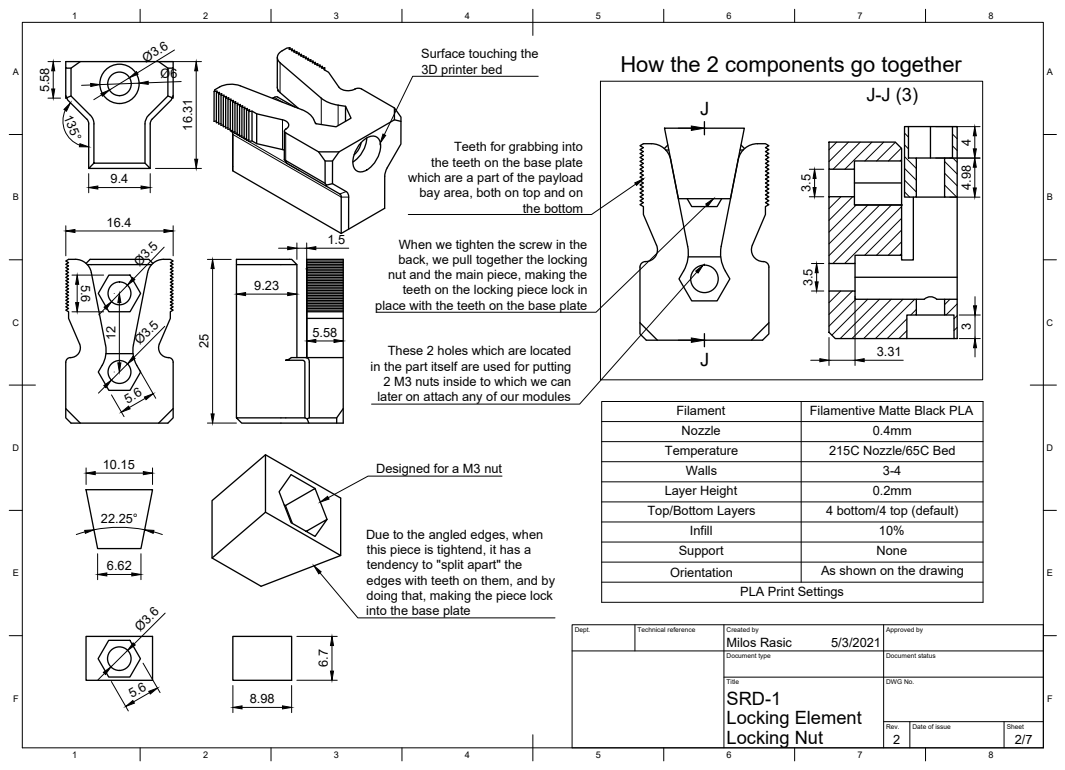
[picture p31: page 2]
8 BCDEF; ABCDEF; Title; DWG No.; Locking Nut; Locking Element; Milos Rasic JJ; the bottom; into the base plate

Surface touching the
3D printer bed

How the 2 components go together

Teeth for grabbing into
the teeth on the base plate
which are a part of the payload
bay area, both on top and on

When we tighten the screw in the
back, we pull together the locking
nut and the main piece, making the
teeth on the locking piece lock in
place with the teeth on the base plate

These 2 holes which are located
in the part itself are used for putting
2 M3 nuts inside to which we can
later on attach any of our modules

Filament | Filamentive Matte Black PLA
Nozzle | 0.4mm
Temperature | 215C Nozzle/65C Bed
Walls | 3-4
Layer Height | 0.2mm
Top/Bottom Layers | 4 bottom/4 top (default)

Designed for a M3 nut

Due to the angled edges, when
this piece is tightend, it has a
tendency to "split apart" the
edges with teeth on them, and by
doing that, making the piece lock

Infill | 10%
Support | None
Orientation | As shown on the drawing

PLA Print Settings

Dept. | Technical reference | Created by 5/3/2021 | Approved by

Document type | Document status

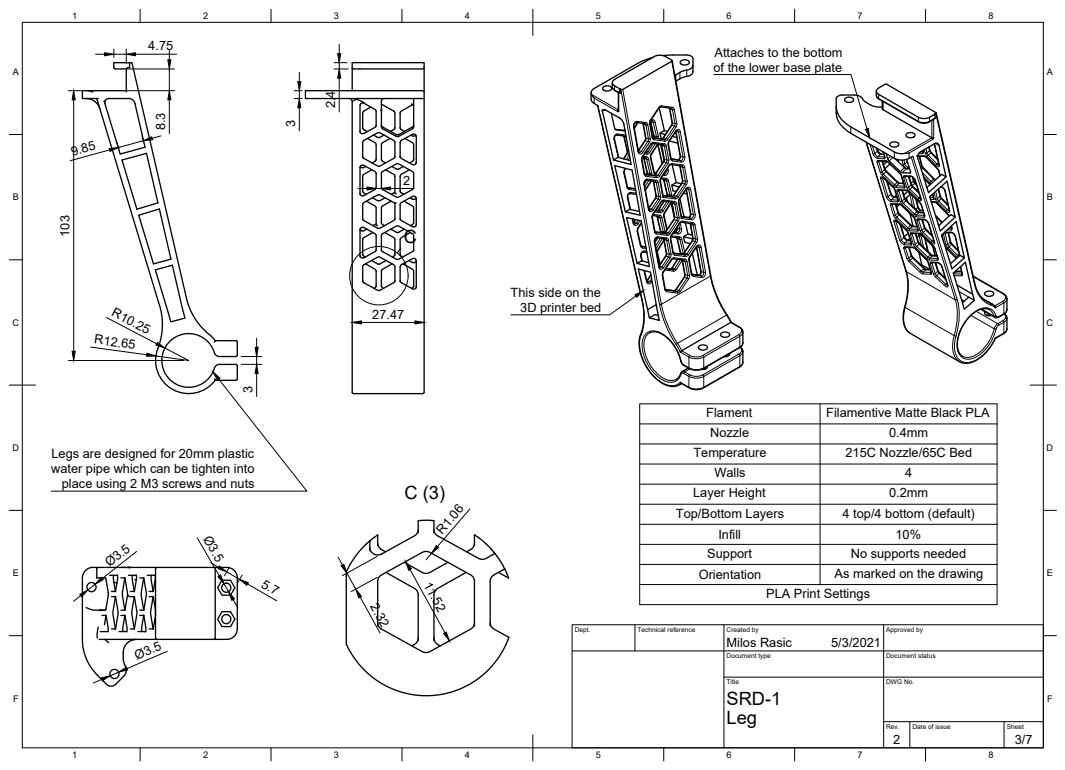
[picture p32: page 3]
Title; DWG No.

Attaches to the bottom
of the lower base plate

This side on the
3D printer bed

Flament | Filamentive Matte Black PLA
Nozzle | 0.4mm
Temperature | 215C Nozzle/65C Bed
Walls | 4
Layer Height | 0.2mm
Top/Bottom Layers | 4 top/4 bottom (default)

Legs are designed for 20mm plastic
water pipe which can be tighten into
place using 2 M3 screws and nuts

Infill | 10%
Support | No supports needed
Orientation | As marked on the drawing

11.52 PLA Print Settings

Dept. | Technical reference | Created by Milos Rasic 5/3/2021 | Approved by

Document type | Document status

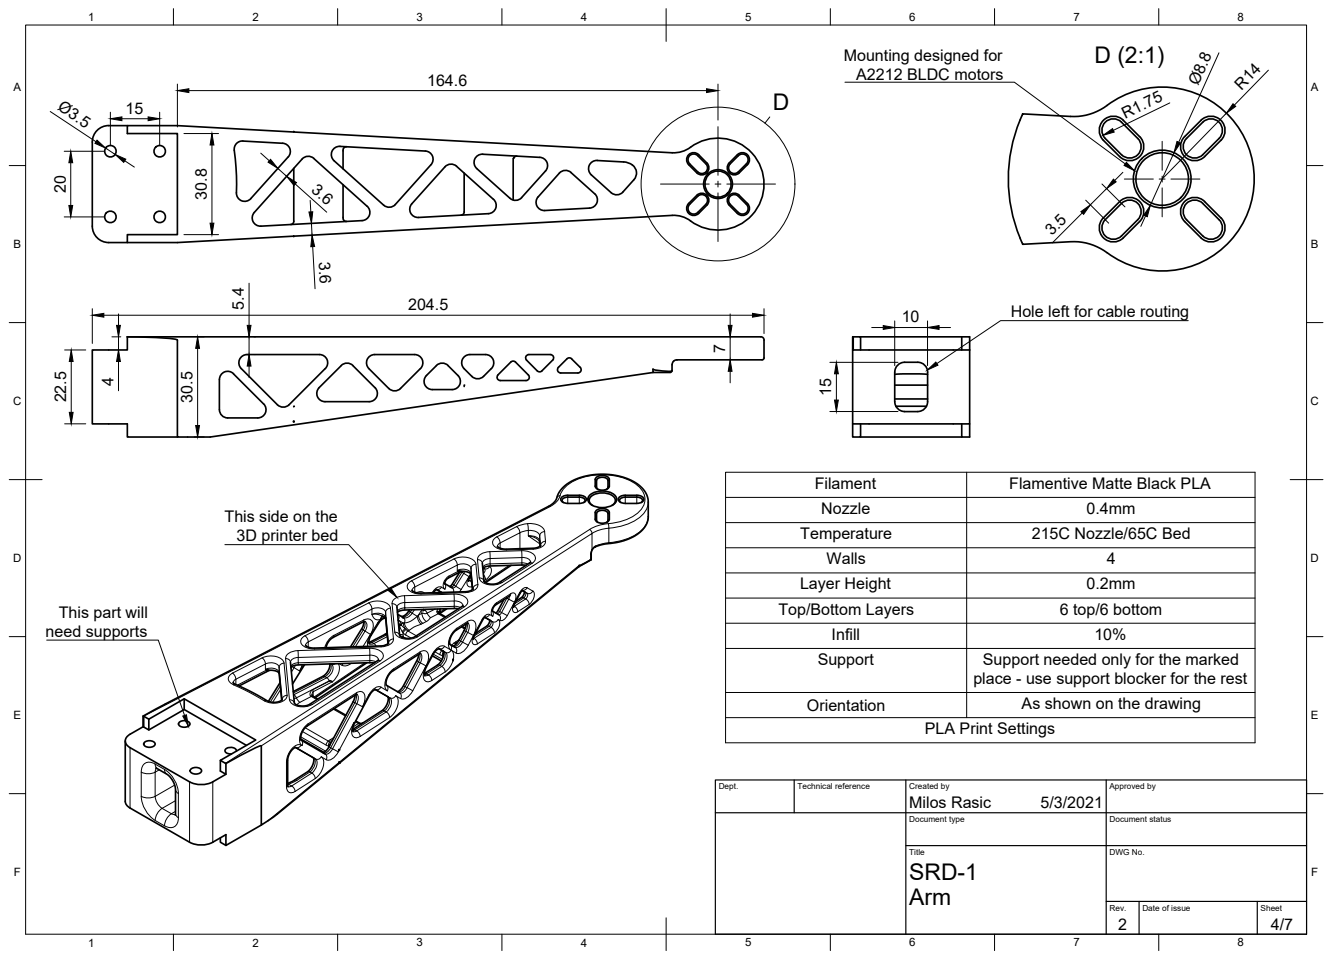
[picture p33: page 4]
Title; DWG No.

Mounting designed for
A2212 BLDC motors

Hole left for cable routing

Filament | Flamentive Matte Black PLA
Nozzle | 0.4mm
Temperature | 215C Nozzle/65C Bed
Walls | 4
Layer Height | 0.2mm
Top/Bottom Layers | 6 top/6 bottom

This side on the
3D printer bed

This part will
need supports

Infill | 10%
Support | Support needed only for the marked place - use support blocker for the rest

Orientation | As shown on the drawing

PLA Print Settings

Dept. | Technical reference | Created by Milos Rasic 5/3/2021 | Approved by

Document type | Document status

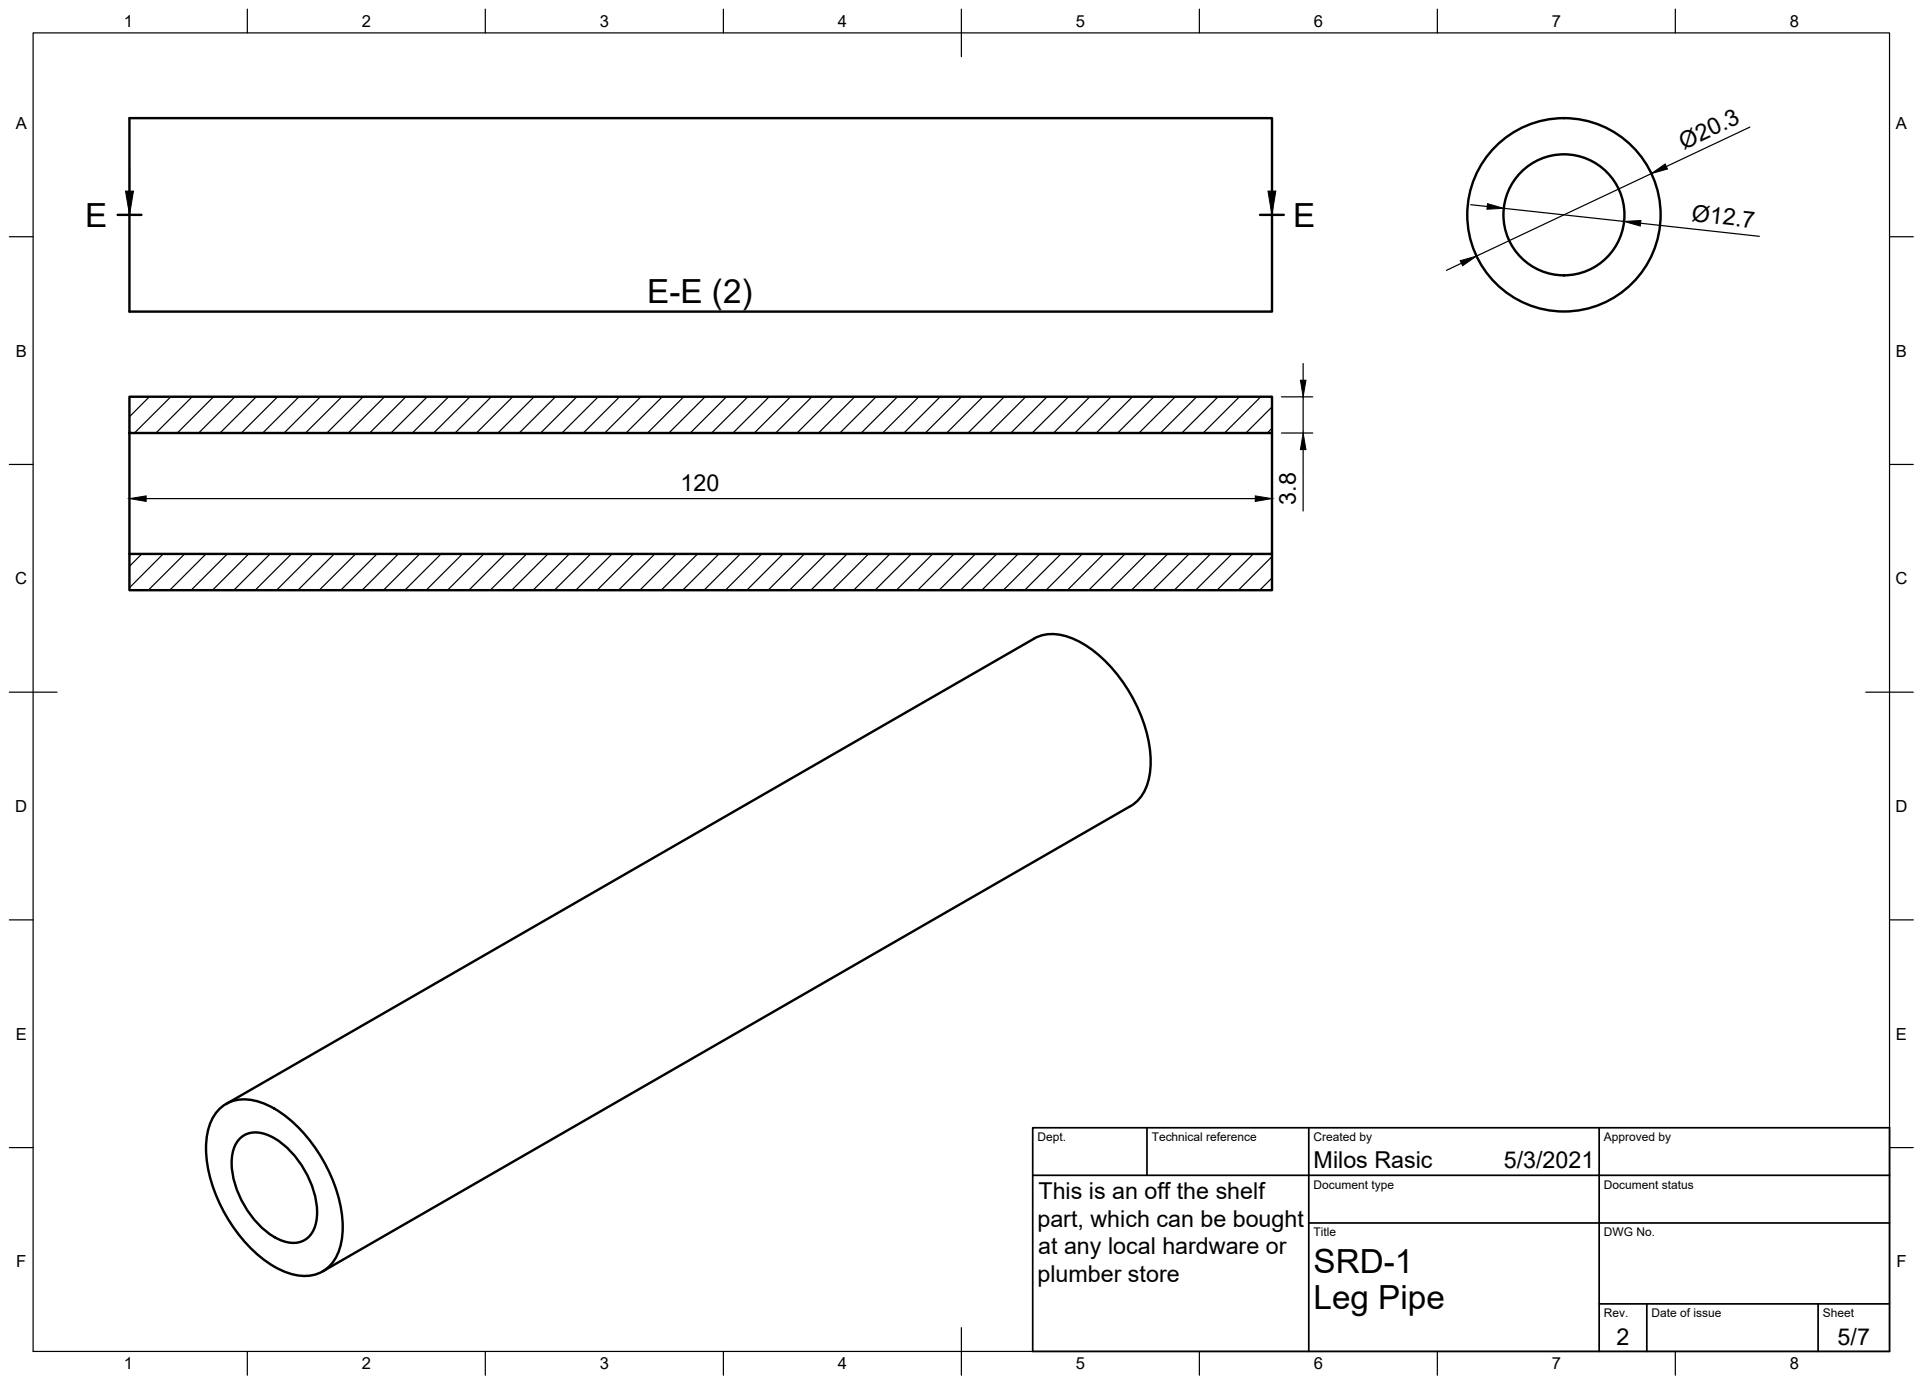
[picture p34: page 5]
Title; DWG No.; Leg Pipe

Dept. | Technical reference | Created by Milos Rasic 5/3/2021 | Approved by

This is an off the shelf
part, which can be bought
at any local hardware or
plumber store

Document type | Document status

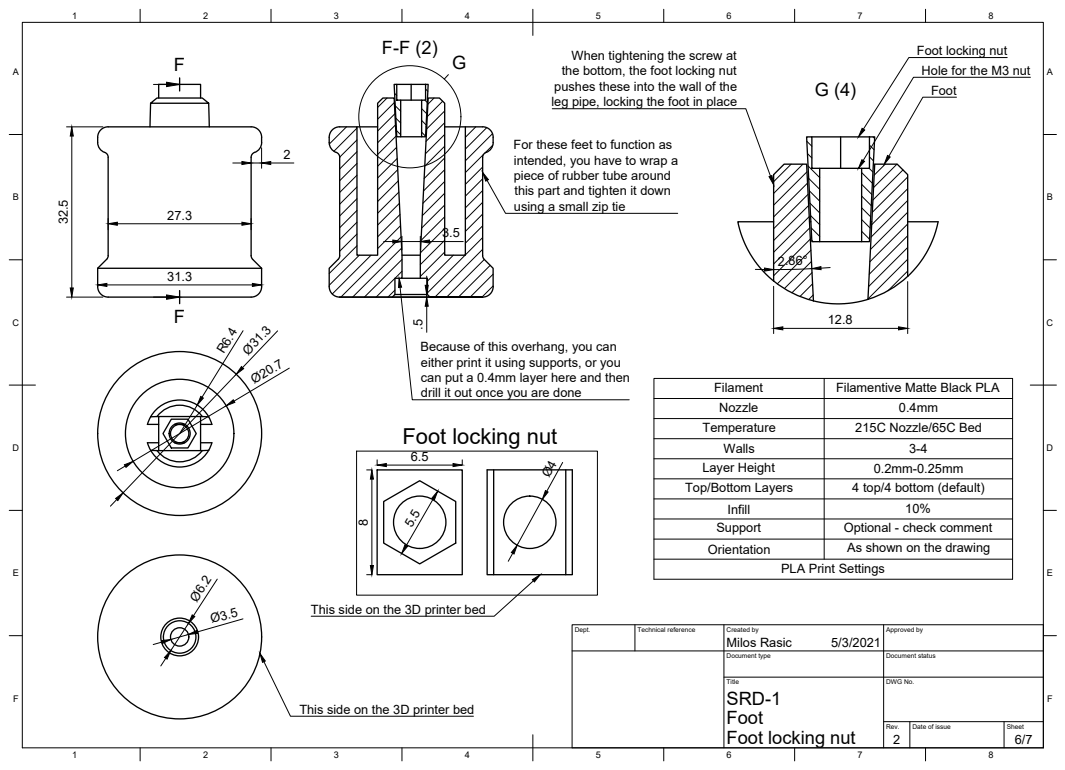
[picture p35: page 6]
Title; DWG No.; Foot locking nut; Filament; Filamentive Matte Black PLA .5

When tightening the screw at
the bottom, the foot locking nut
pushes these into the wall of the
leg pipe, locking the foot in place

Foot locking nut
Hole for the M3 nut
Foot

For these feet to function as
intended, you have to wrap a
piece of rubber tube around
this part and tighten it down
using a small zip tie

Because of this overhang, you can
either print it using supports, or you
can put a 0.4mm layer here and then
drill it out once you are done

Nozzle | 0.4mm
Temperature | 215C Nozzle/65C Bed
Walls | 3-4
Layer Height | 0.2mm-0.25mm
Top/Bottom Layers | 4 top/4 bottom (default)

Infill | 10%
Support | Optional - check comment
Orientation | As shown on the drawing

PLA Print Settings

This side on the 3D printer bed

Dept. | Technical reference | Created by Milos Rasic 5/3/2021 | Approved by

Document type | Document status

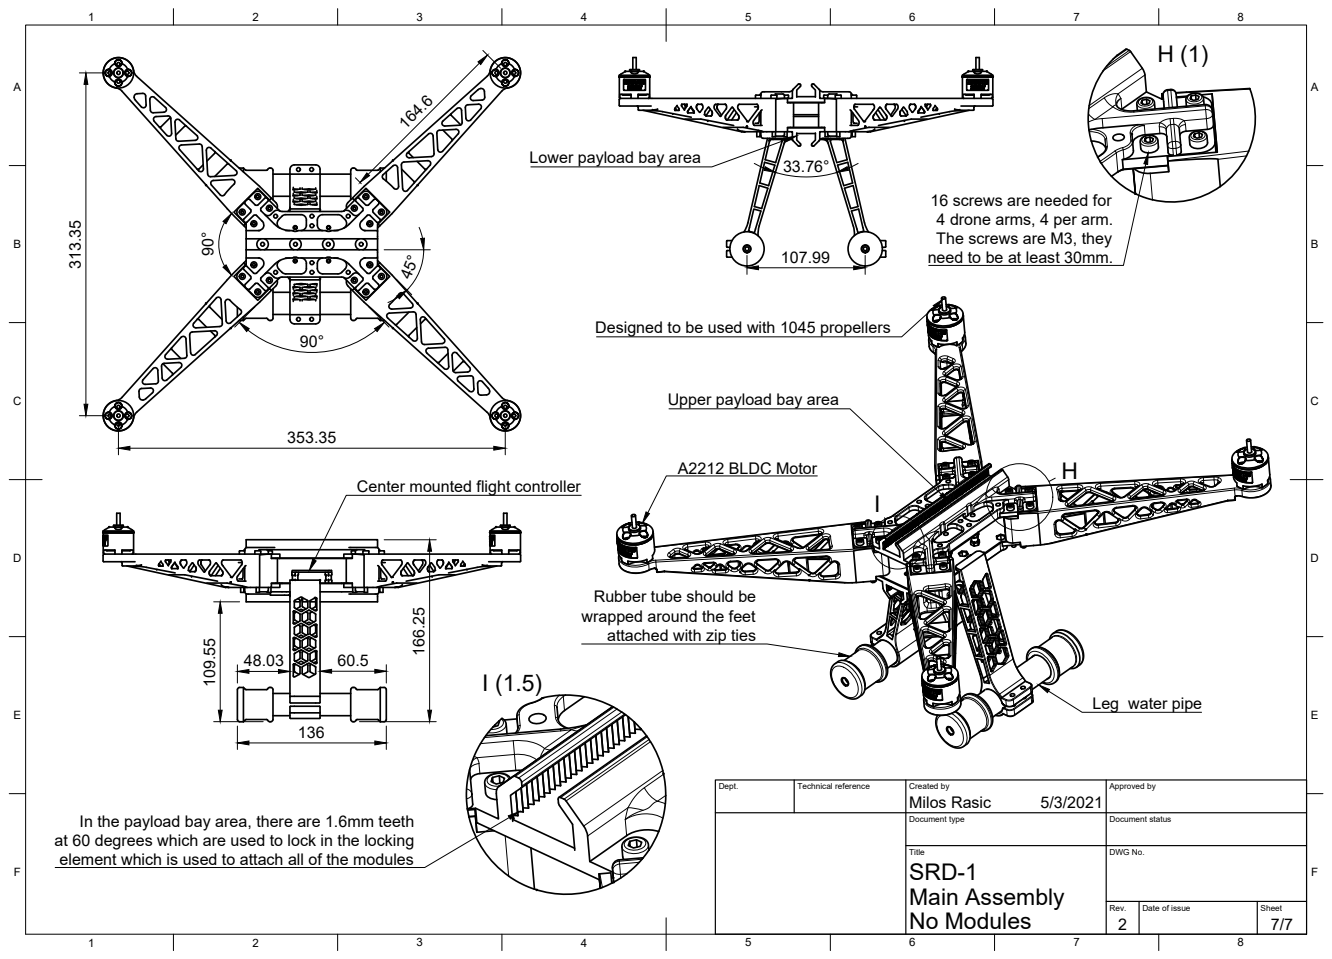
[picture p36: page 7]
Dept.; Technical reference; Created by; Approved by; Document type; Document status; Title; DWG No.; No Modules; Main Assembly; Milos Rasic; A2212 BLDC Motor

Lower payload bay area

16 screws are needed for
4 drone arms, 4 per arm.
The screws are M3, they
need to be at least 30mm.

Designed to be used with 1045 propellers

Upper payload bay area

Center mounted flight controller

Rubber tube should be
wrapped around the feet
attached with zip ties

Leg water pipe

In the payload bay area, there are 1.6mm teeth
at 60 degrees which are used to lock in the locking
element which is used to attach all of the modules

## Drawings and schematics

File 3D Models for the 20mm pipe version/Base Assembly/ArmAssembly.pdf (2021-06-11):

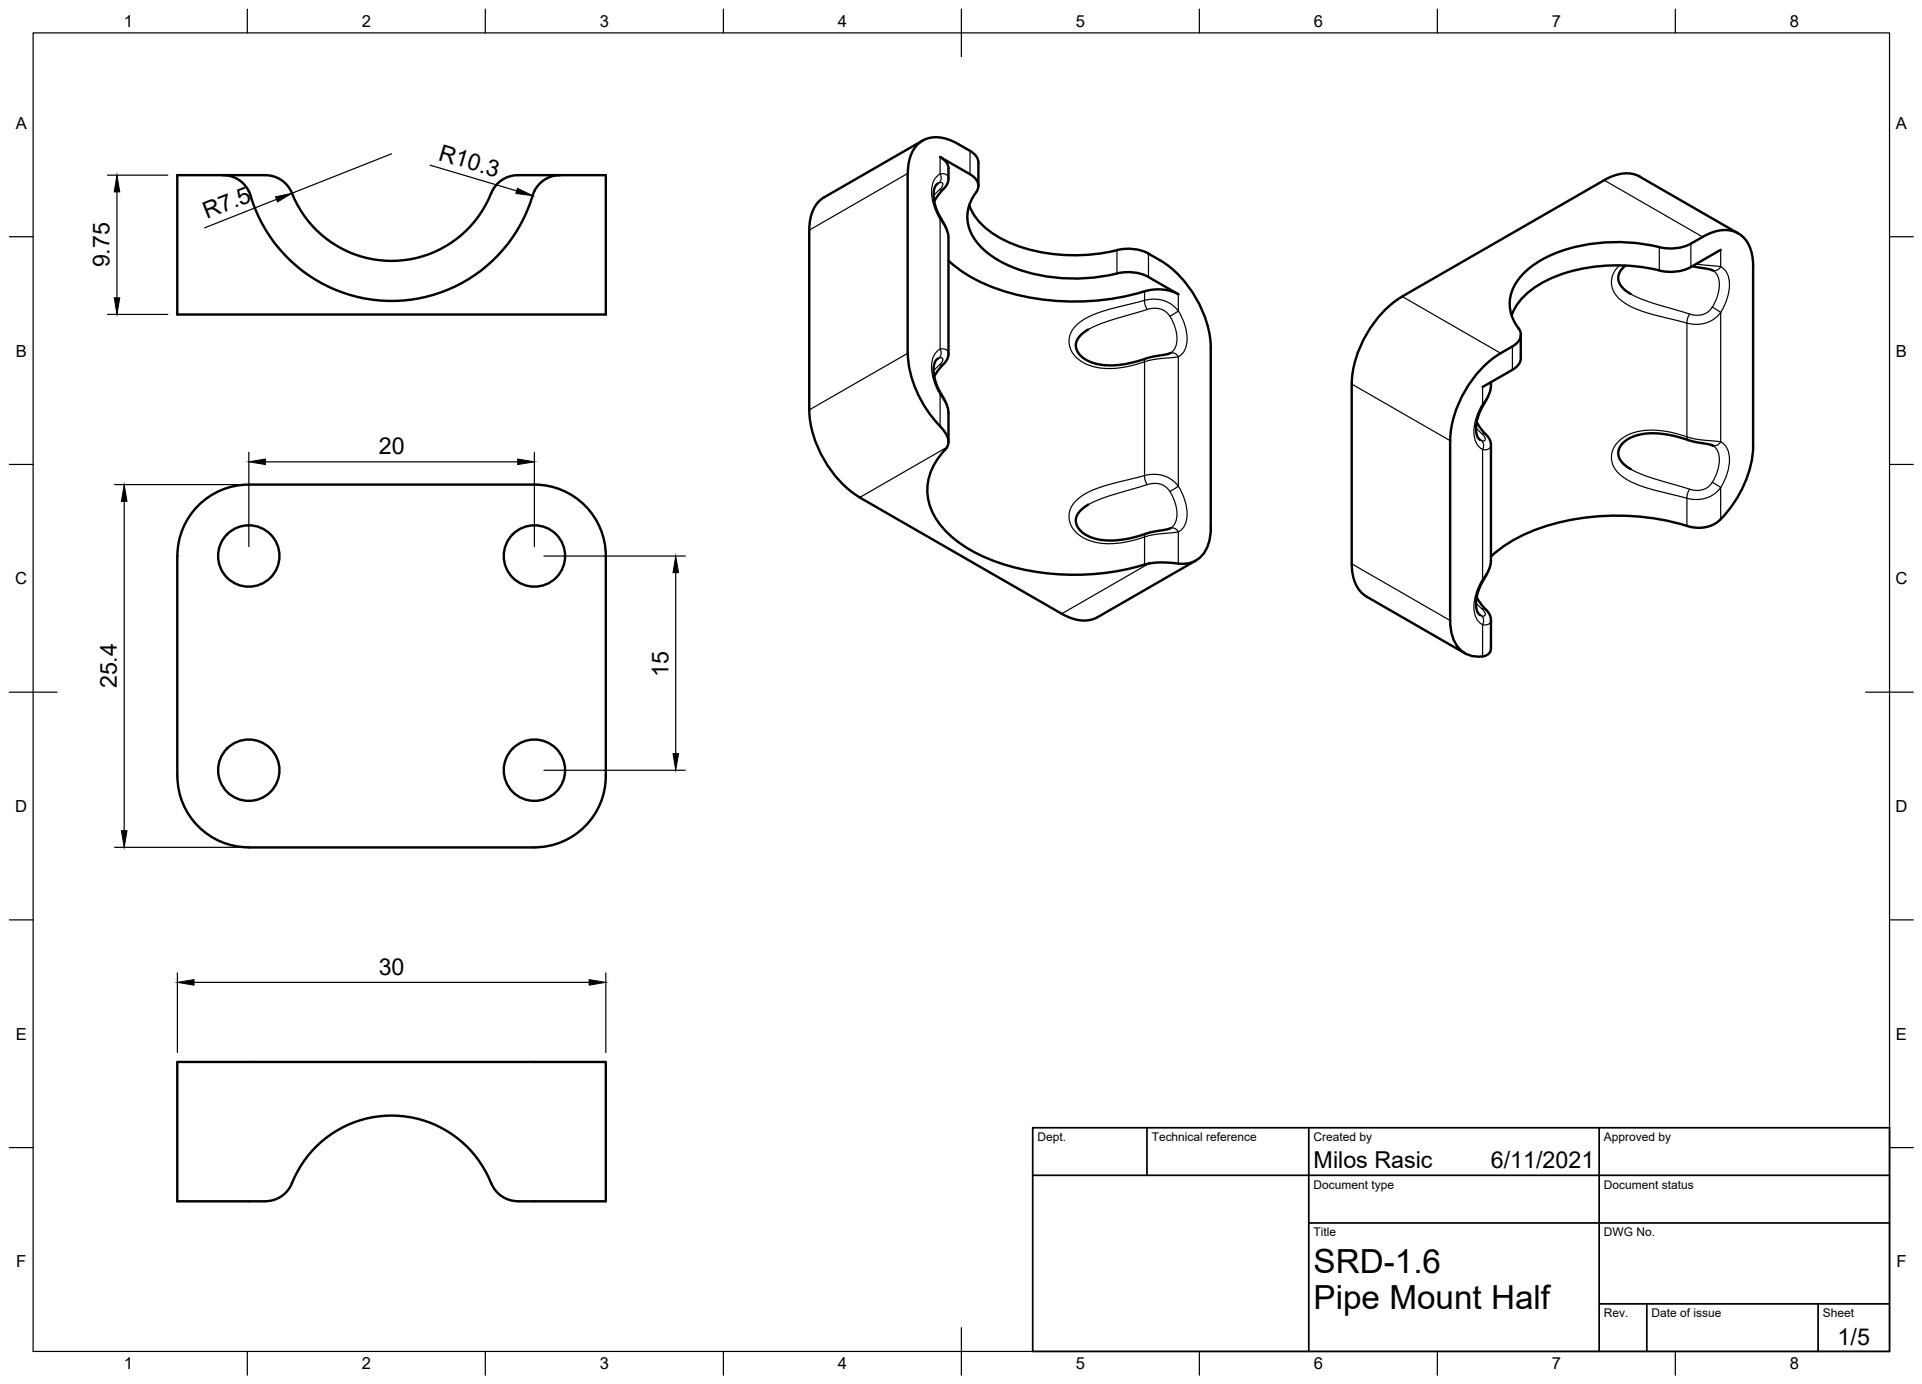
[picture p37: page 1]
Title; DWG No.; Rev.; Date of issue; Sheet

Dept. | Technical reference | Created by Milos Rasic 6/11/2021 | Approved by

Document type | Document status

SRD-1.6
Pipe Mount Half

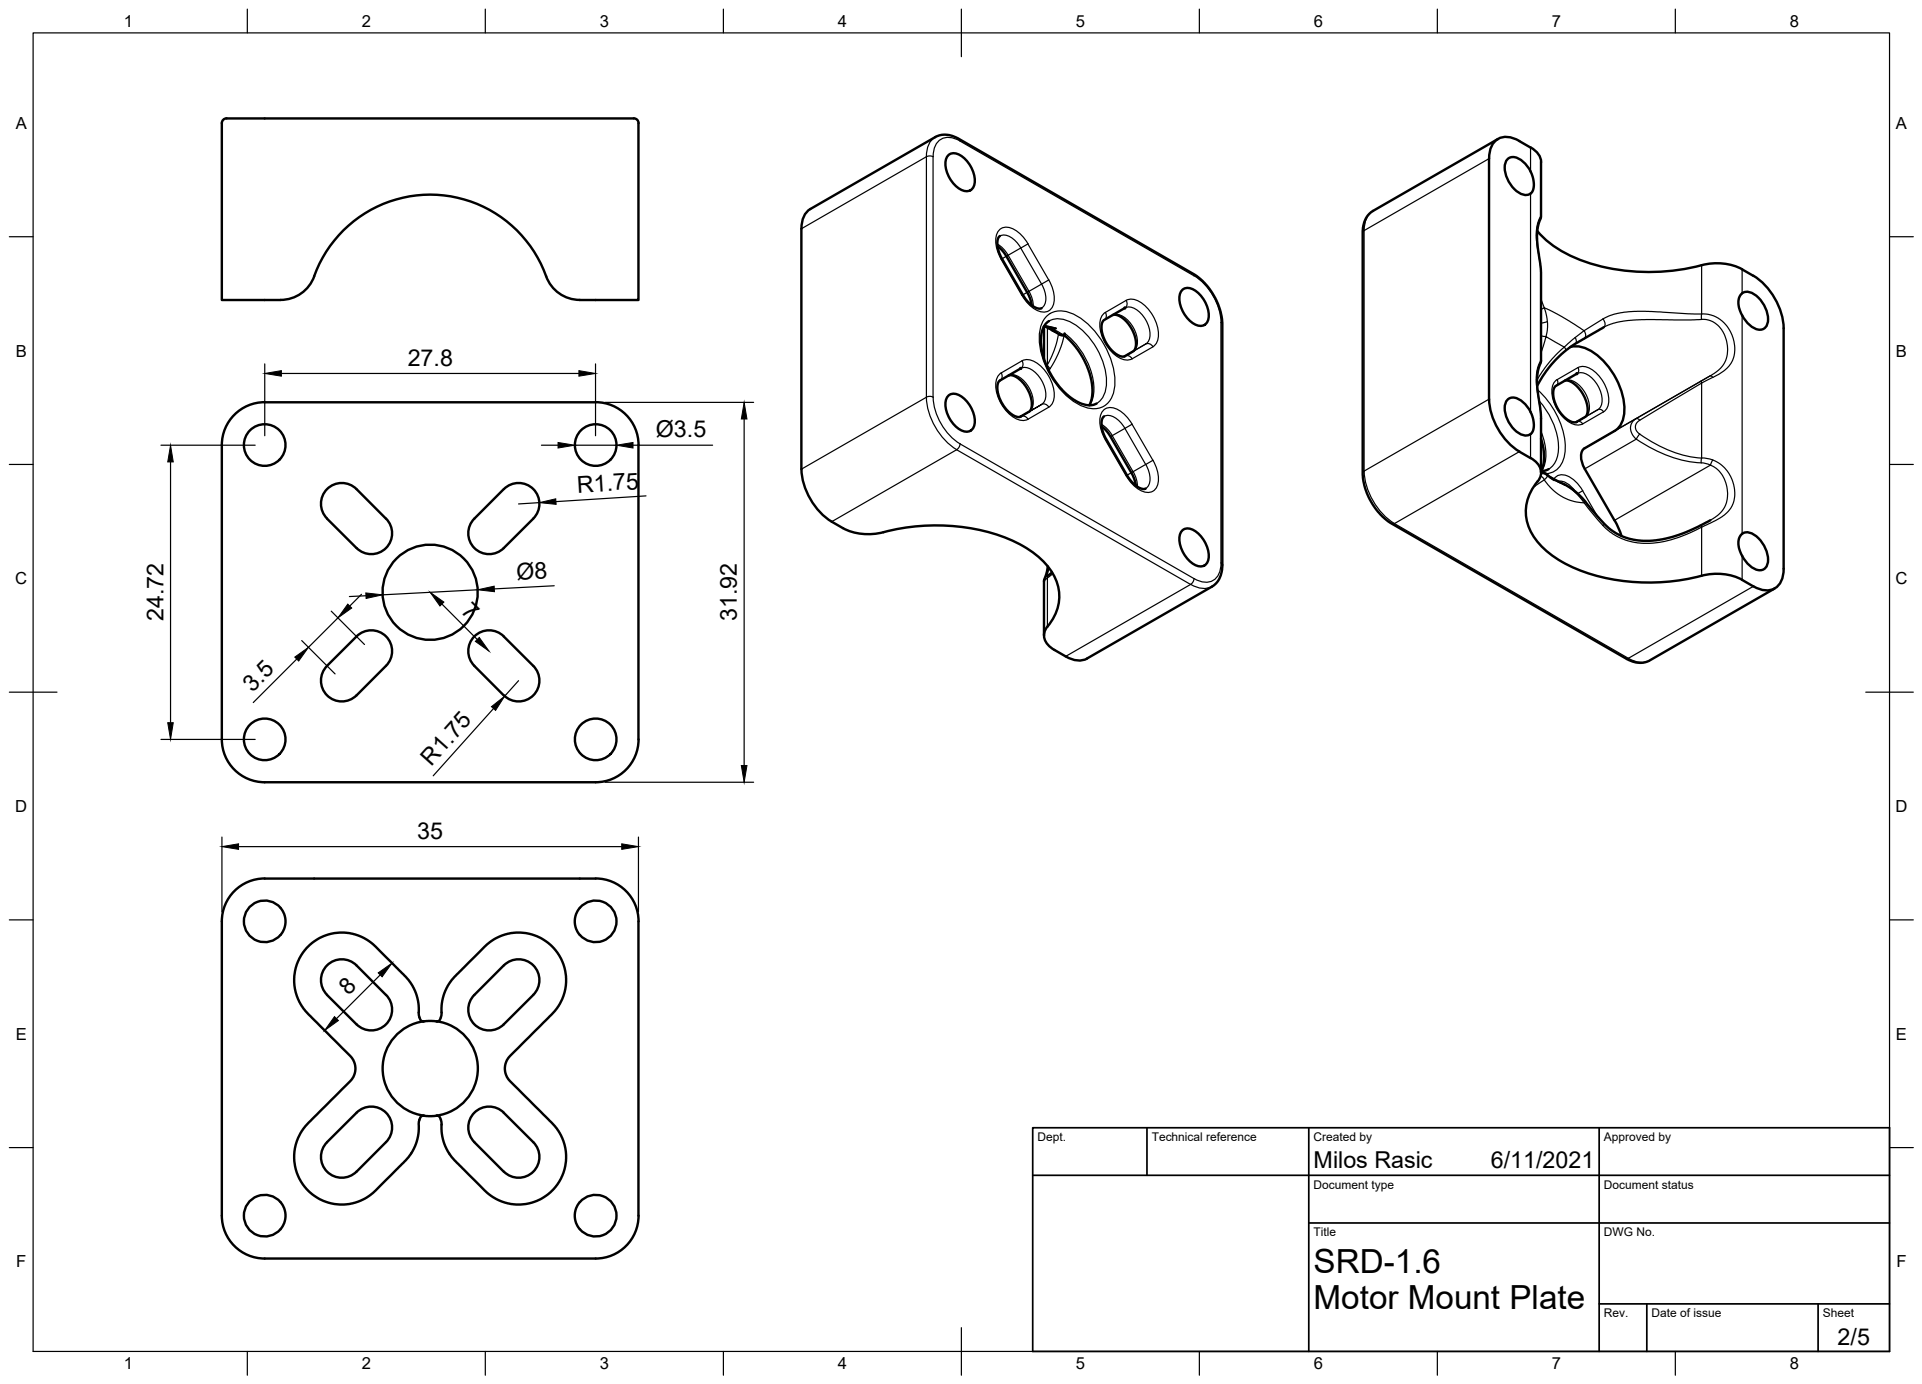
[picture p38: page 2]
Title; DWG No.

Dept. | Technical reference | Created by Milos Rasic 6/11/2021 | Approved by

Document type | Document status

SRD-1.6
Motor Mount Plate

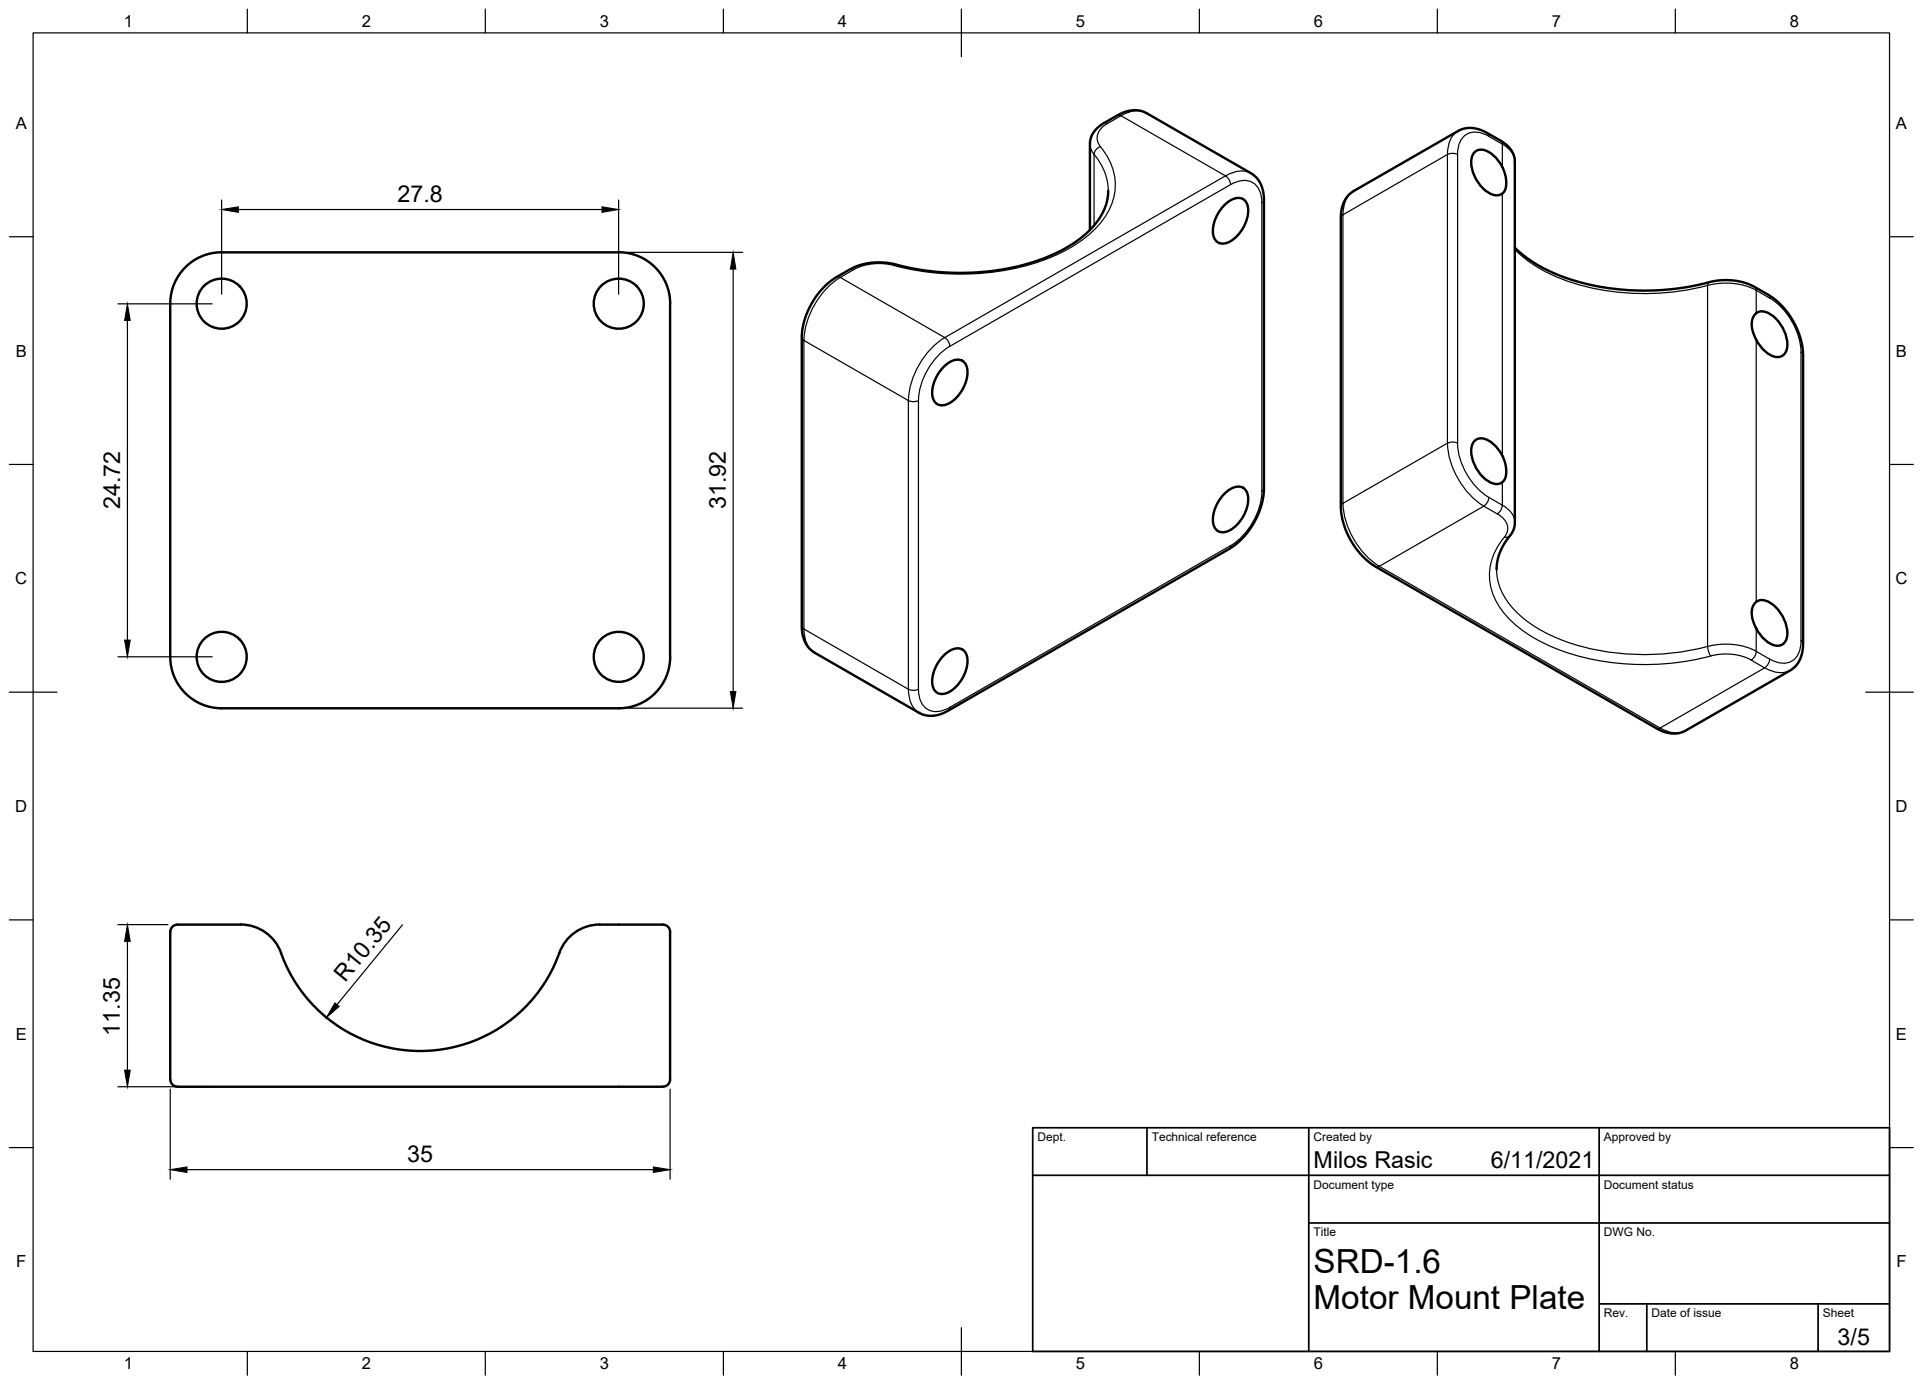
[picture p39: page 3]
Title; DWG No.

Dept. | Technical reference | Created by Milos Rasic 6/11/2021 | Approved by

Document type | Document status

SRD-1.6
Motor Mount Plate

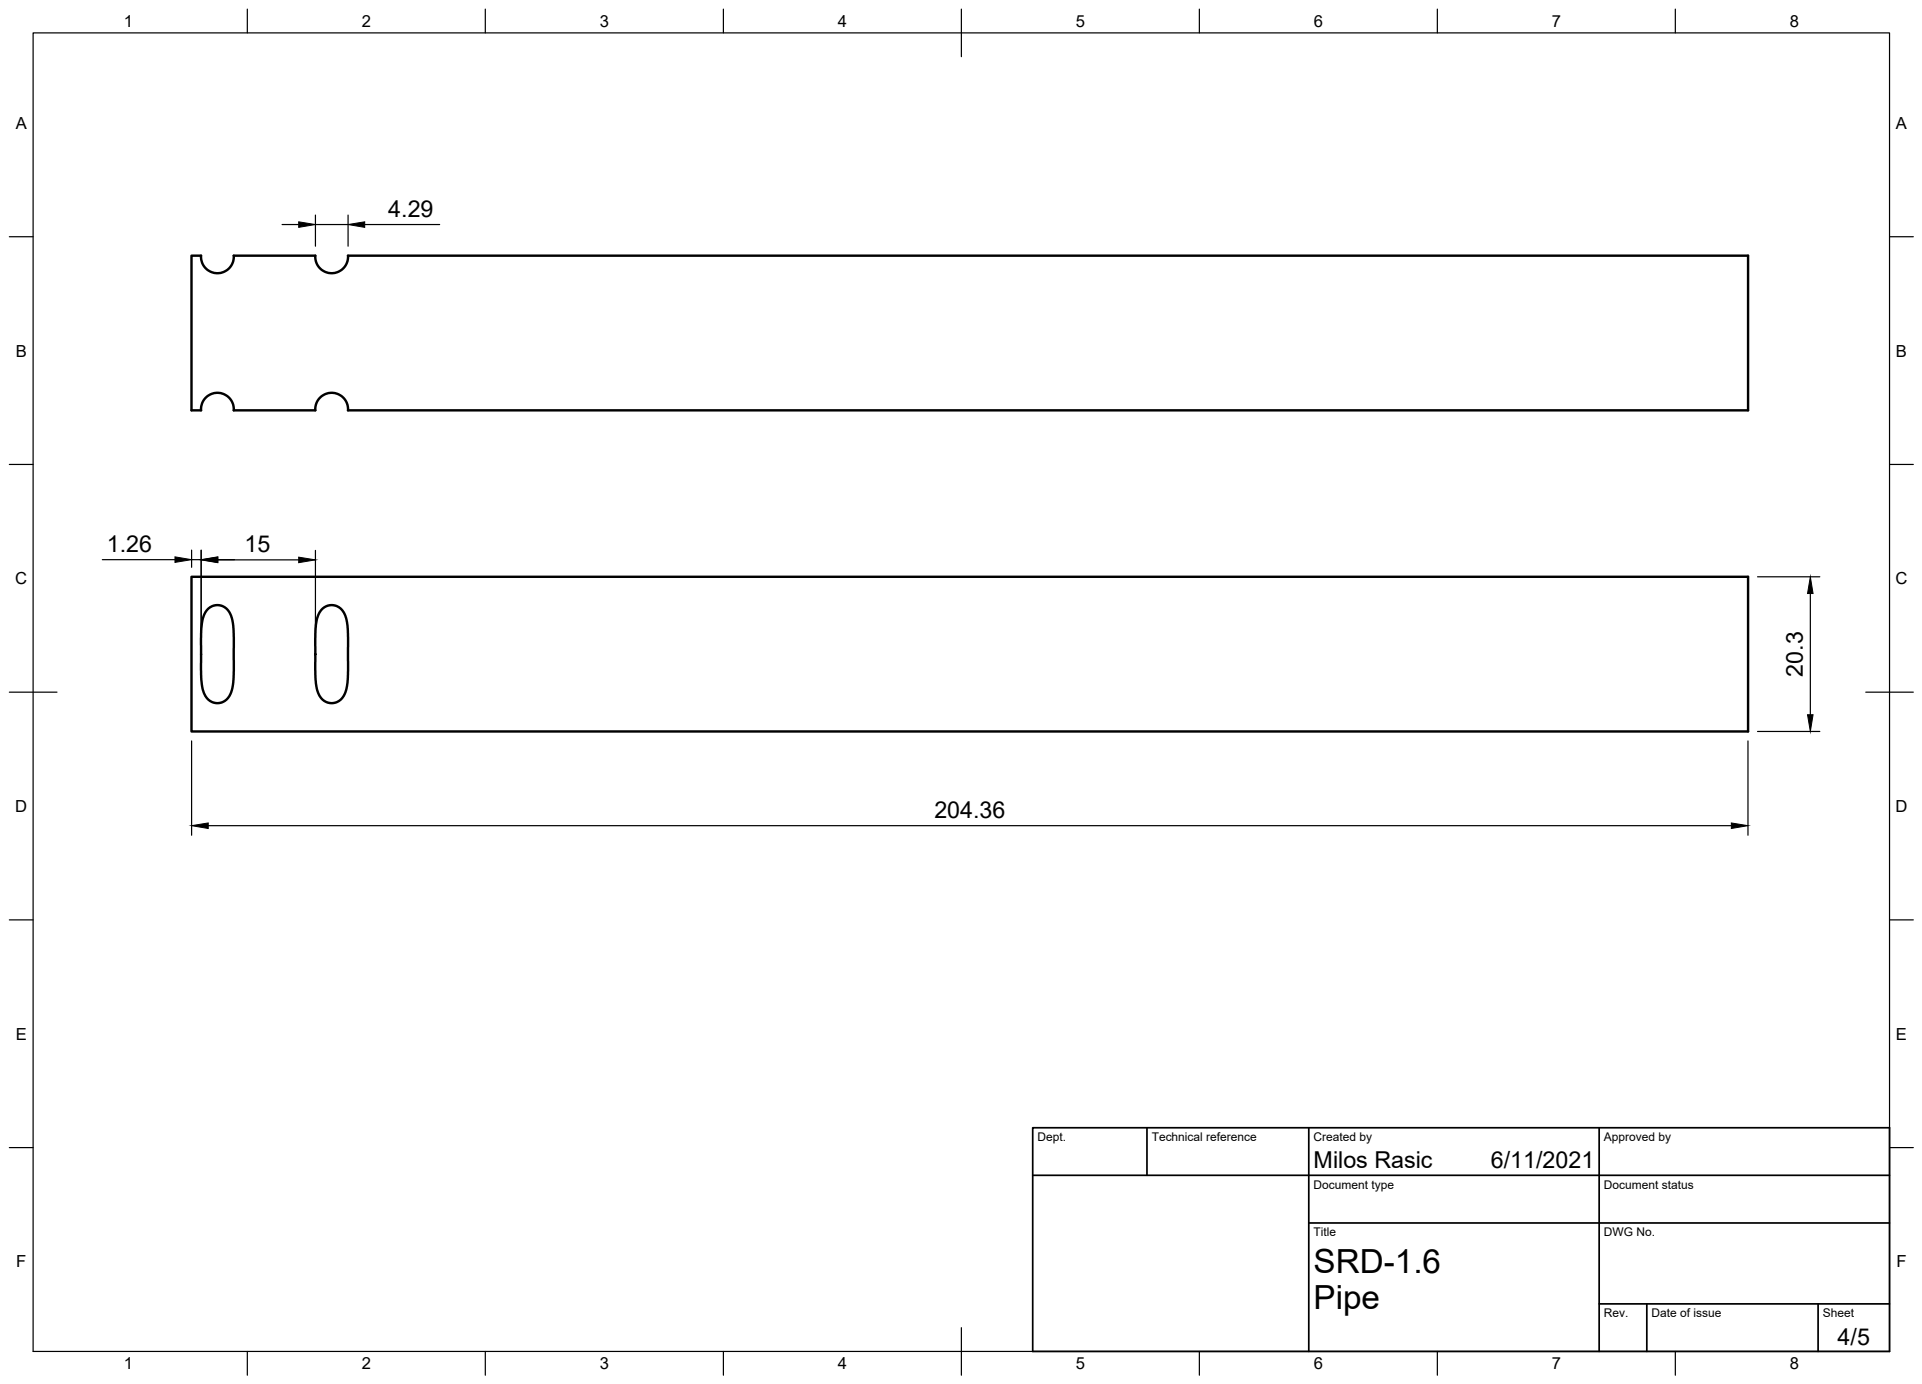
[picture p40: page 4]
Title; DWG No.

Dept. | Technical reference | Created by Milos Rasic 6/11/2021 | Approved by

Document type | Document status

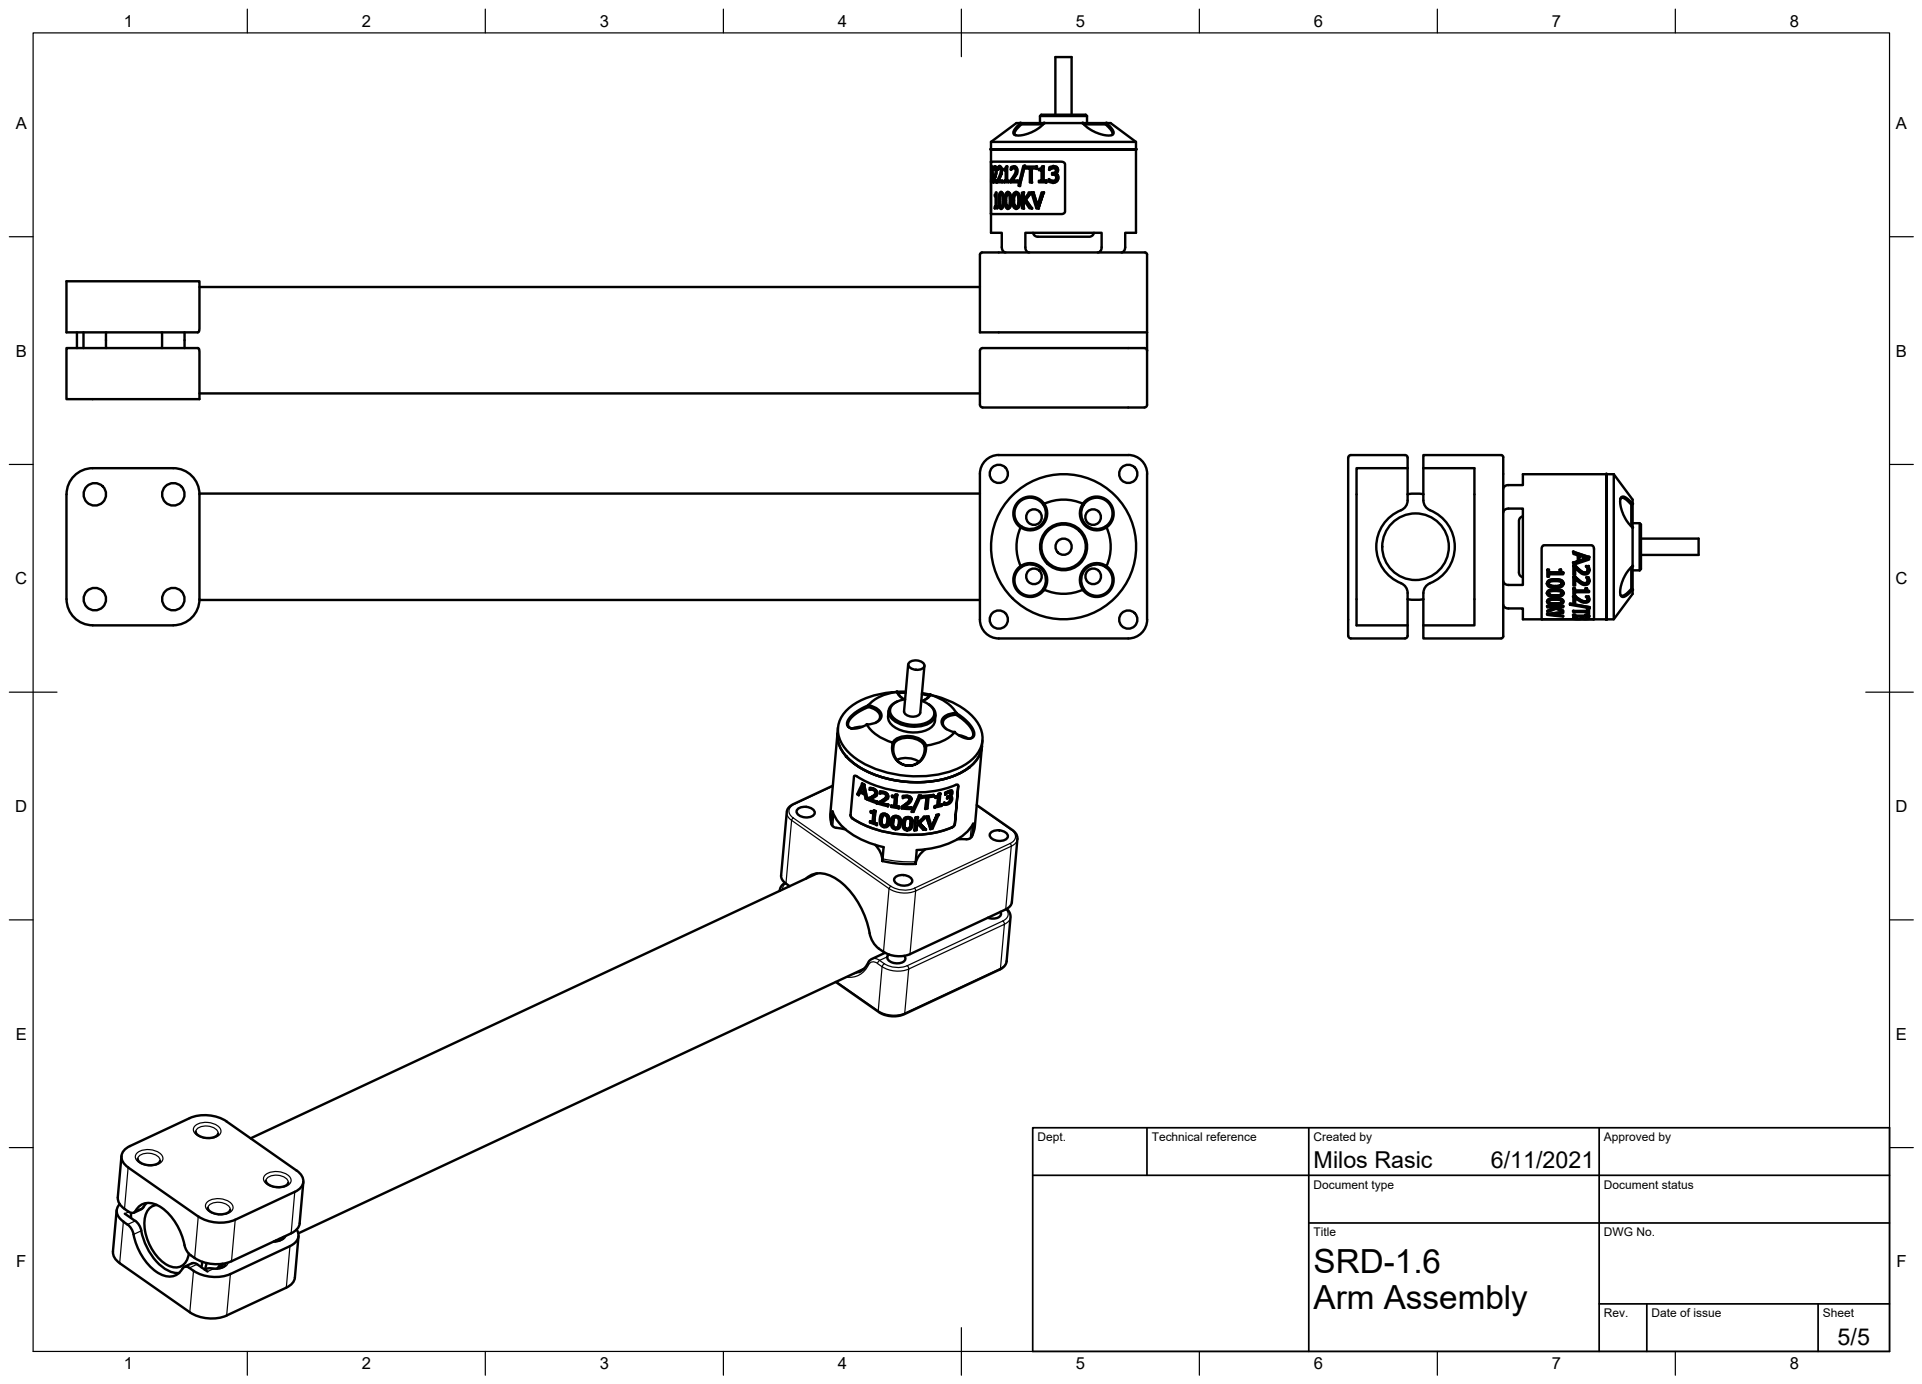
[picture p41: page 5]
Title; DWG No.; Arm Assembly

Dept. | Technical reference | Created by Milos Rasic 6/11/2021 | Approved by

Document type | Document status

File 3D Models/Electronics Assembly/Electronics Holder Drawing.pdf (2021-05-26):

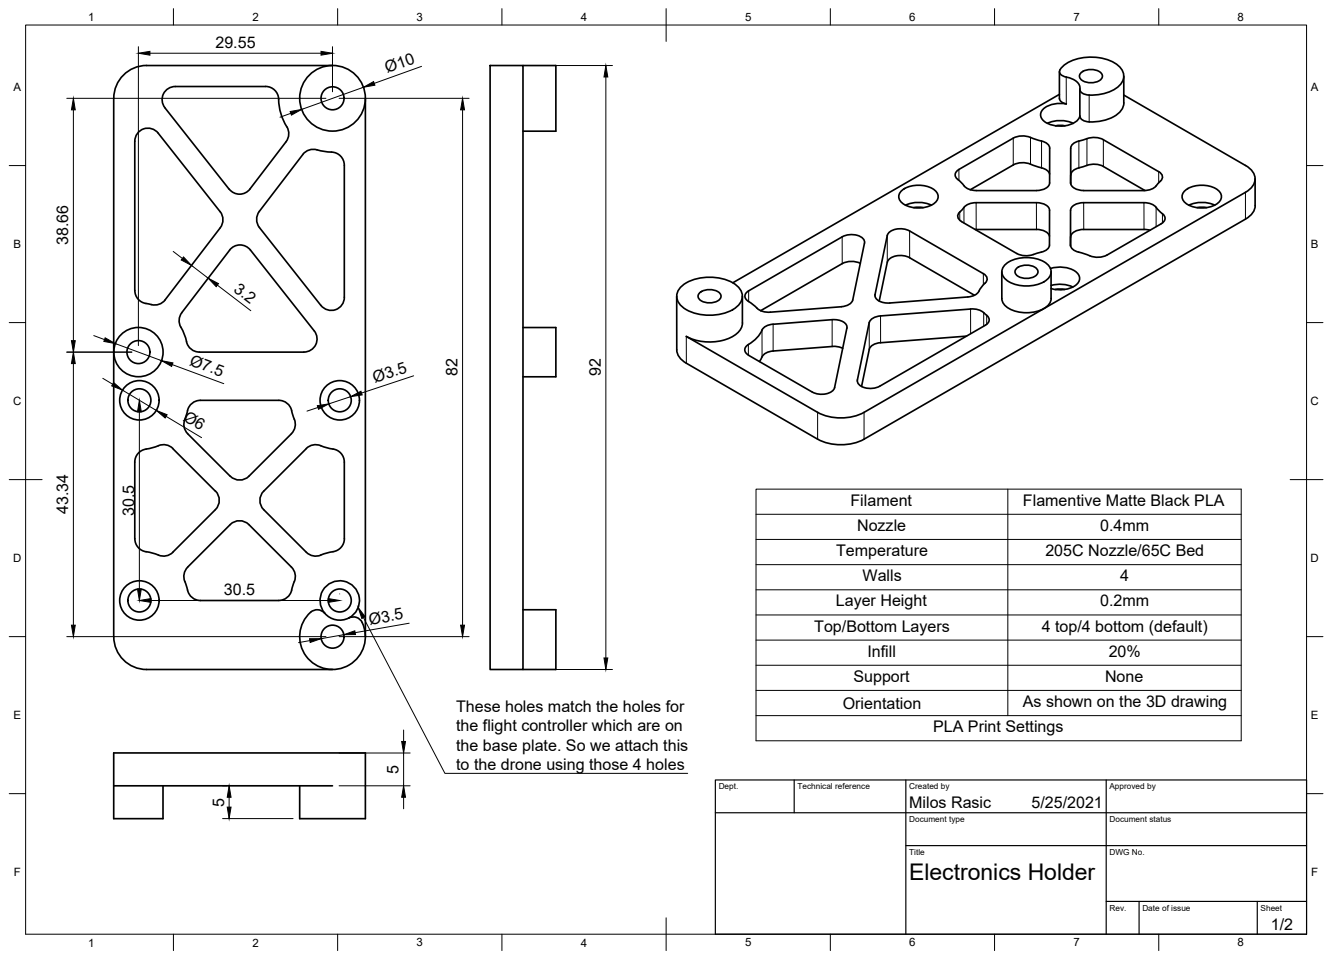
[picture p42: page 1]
Title; DWG No.; Rev.; Date of issue; Sheet; Electronics Holder

Filament | Flamentive Matte Black PLA
Nozzle | 0.4mm
Temperature | 205C Nozzle/65C Bed
Walls | 4
Layer Height | 0.2mm
Top/Bottom Layers | 4 top/4 bottom (default)

Infill | 20%
Support | None
Orientation | As shown on the 3D drawing

These holes match the holes for
the flight controller which are on
the base plate. So we attach this
to the drone using those 4 holes

PLA Print Settings

Dept. | Technical reference | Created by Milos Rasic 5/25/2021 | Approved by

Document type | Document status

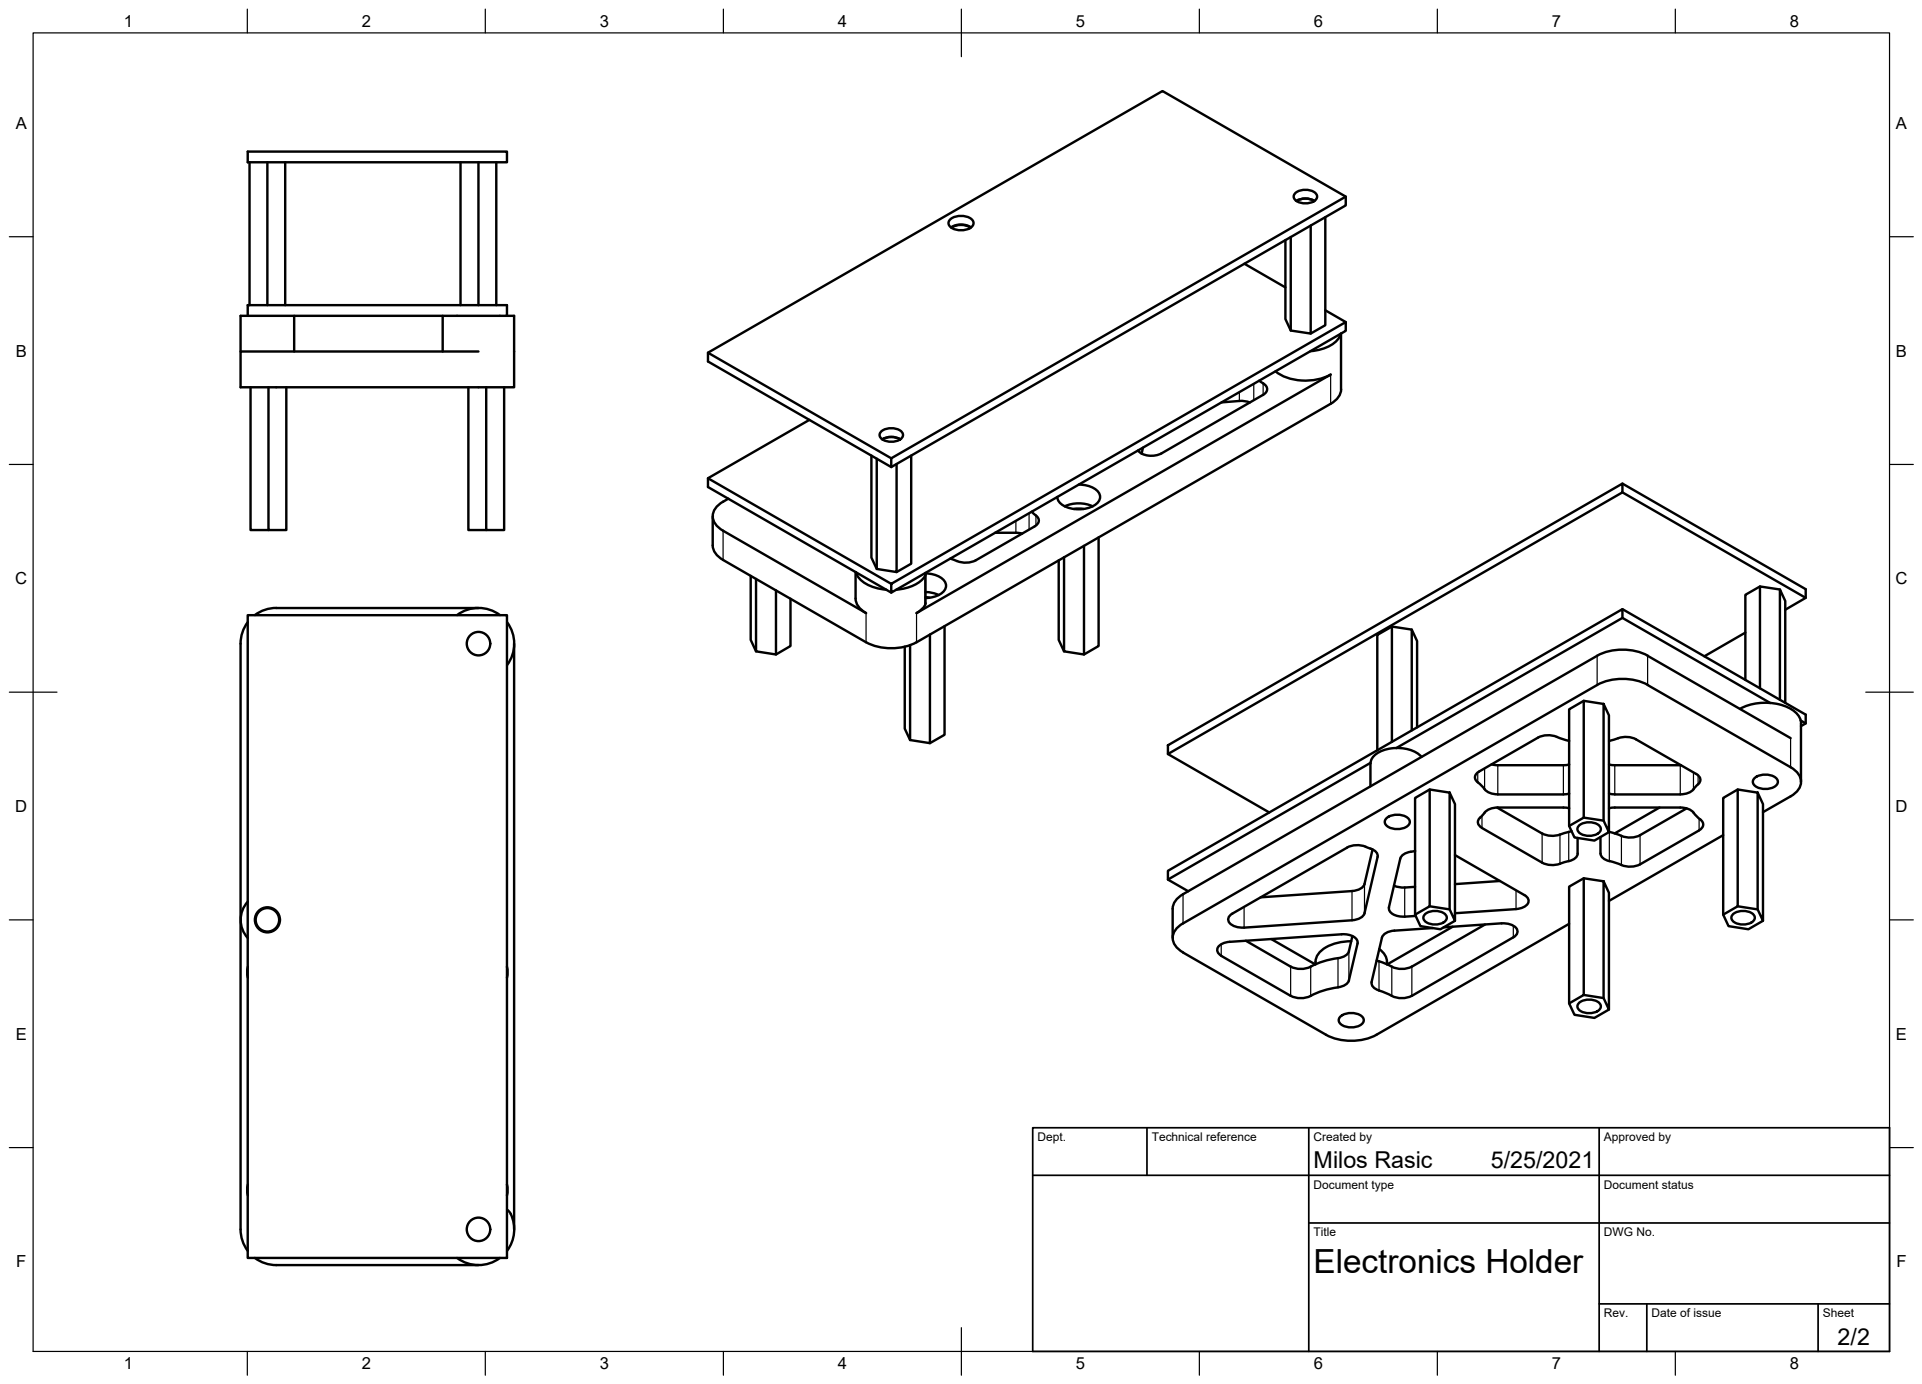
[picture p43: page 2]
Title; DWG No.; Rev.; Date of issue; Sheet; Electronics Holder

Dept. | Technical reference | Created by Milos Rasic 5/25/2021 | Approved by

Document type | Document status

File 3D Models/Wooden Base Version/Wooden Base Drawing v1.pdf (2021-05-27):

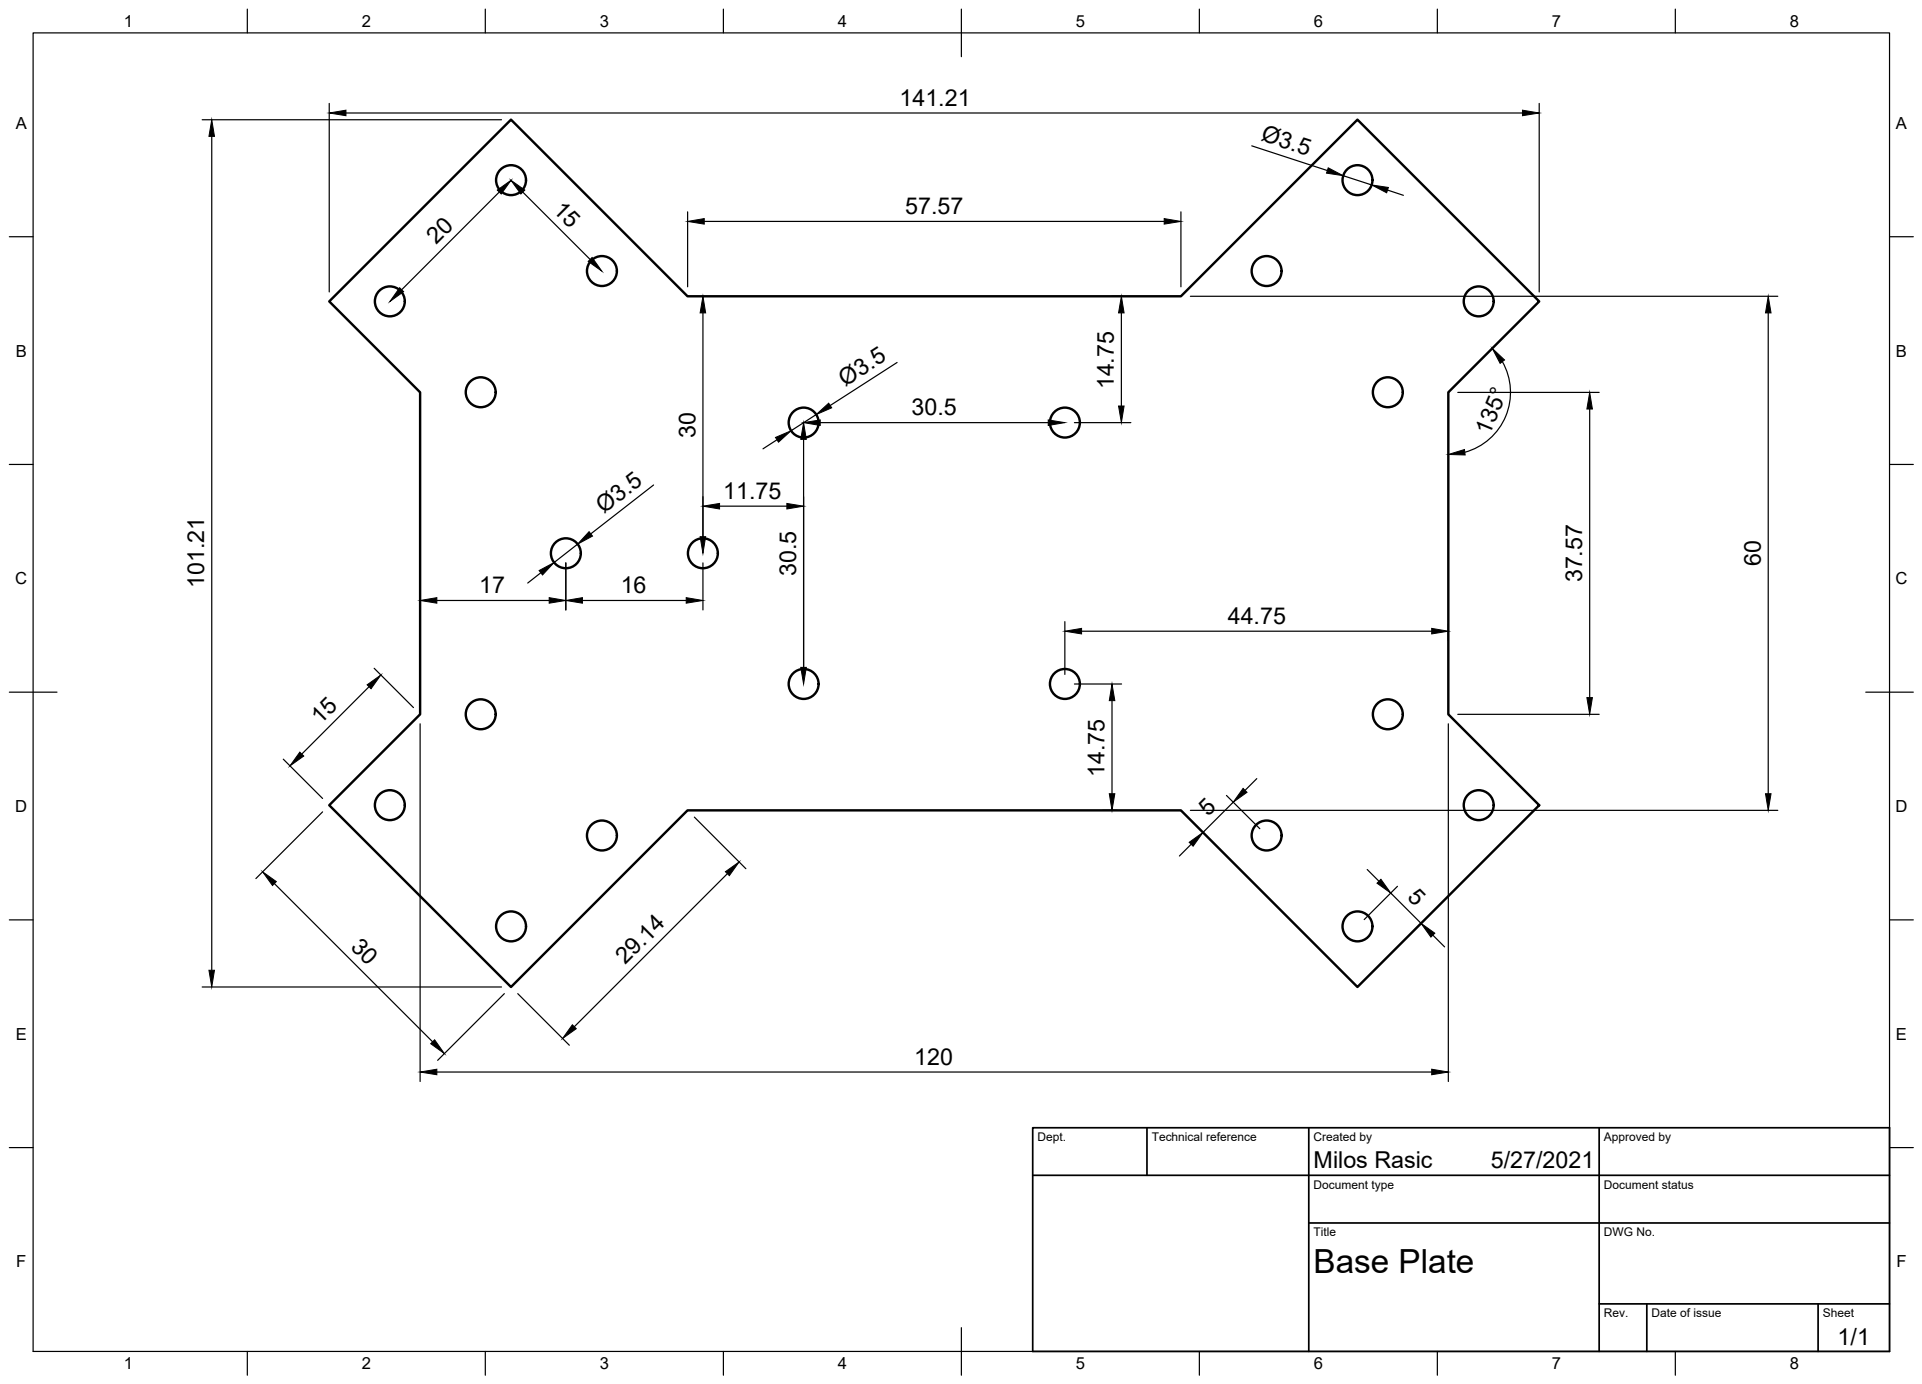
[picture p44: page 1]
Title; DWG No.; Rev.; Date of issue; Sheet; Base Plate

Dept. | Technical reference | Created by Milos Rasic 5/27/2021 | Approved by

Document type | Document status

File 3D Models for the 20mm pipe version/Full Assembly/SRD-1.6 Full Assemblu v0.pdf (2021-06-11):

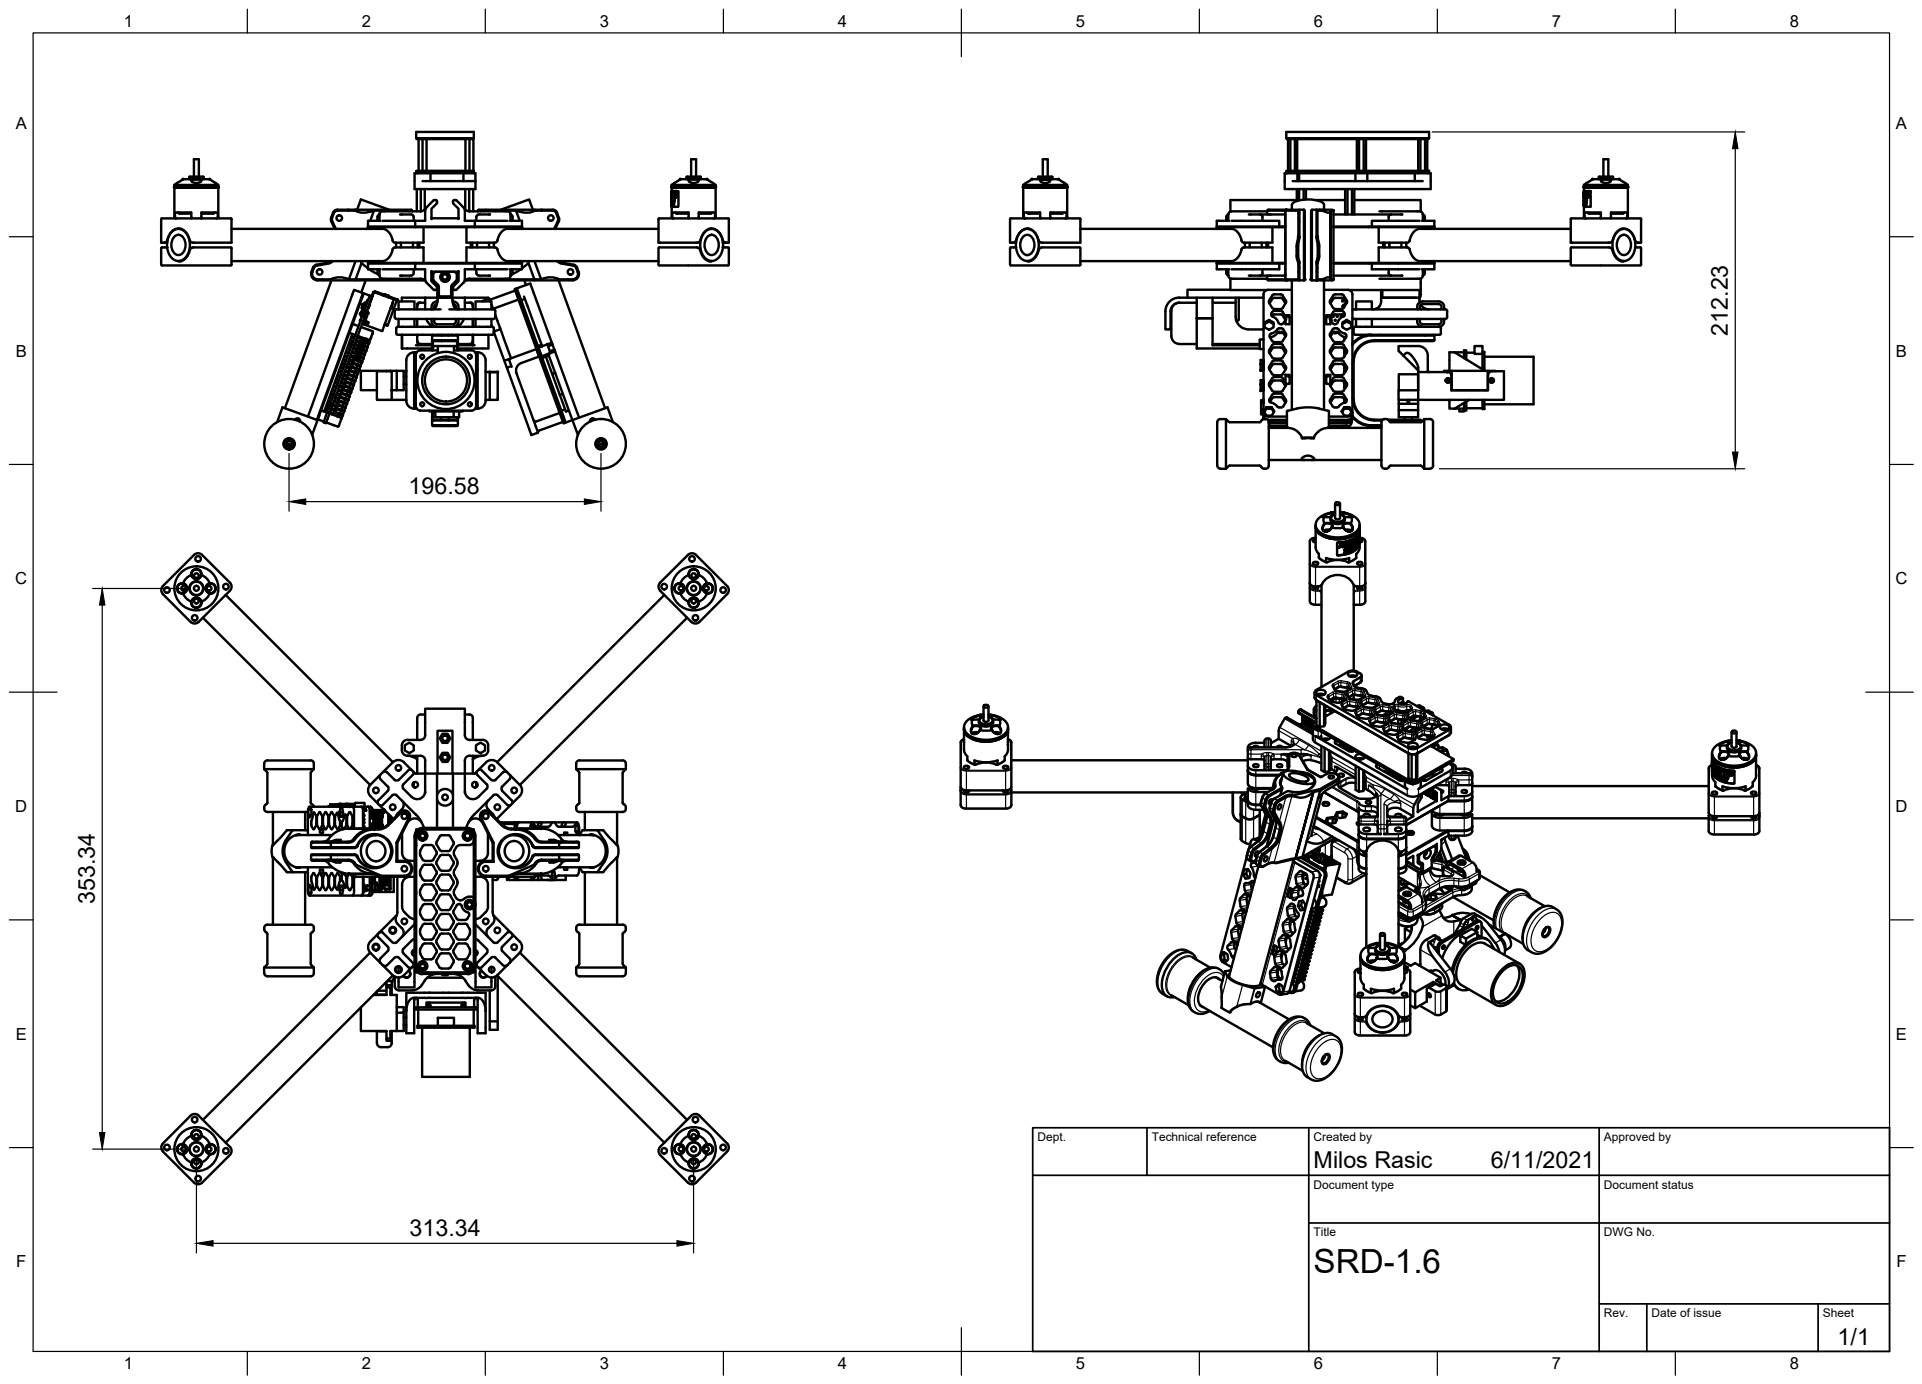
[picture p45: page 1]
Dept.; Technical reference; Created by; Approved by; Document type; Document status; Title; DWG No.; Rev.; Date of issue; Sheet; Milos Rasic 353.34

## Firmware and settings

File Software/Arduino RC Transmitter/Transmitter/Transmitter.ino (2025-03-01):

// TRANSMITTER CODE

/* 
 *  This code will be used for sending data using the NRF24 to the Arduino on our drone
 *  
 *  Connections for this transmitter are:
 *  NRF24 - standard SPI connection and the other 2 pins to pins 7 & 8
 *  All of the switches are connected to digital pins, they are wires up so they pull the input to ground,
 *  this is so we can use an internall pullup on Arduino pins
 *  On the analog pins we have all of the joysticks from our transmitter
 *  A4 and A5 are left unconnected so we can have I2C devices further on if we desire
 *  
 */
 

/* 
 *  This code is a modified version of the code from Electronoobs.com
 *  Check out his tutorial on the Arduino Drone
 *  
 */
 
#include <SPI.h>
#include <nRF24L01.h>
#include <RF24.h>

#define Pin_AUX1 2
#define Pin_AUX2 3
#define Pin_AUX3 4
#define Pin_AUX4 5
#define Pin_AUX5 6
#define Pin_AUX6 9
#define Pin_AUX7 10

/*Create a unique pipe out. The receiver has to 
  wear the same unique code*/
  
const uint64_t pipeOut = 0xE8E8F0F0E1LL;

RF24 radio(7, 8); // select  CSN  pin

// The sizeof this struct should not exceed 32 bytes
// This gives us up to 32 8 bits channals
struct MyData {
  byte throttle;
  byte yaw;
  byte pitch;
  byte roll;
  byte AUX1;
  byte AUX2;
  byte AUX3;
  byte AUX4;
  byte AUX5;
  byte AUX6;
  byte AUX7;
  byte gimbalY;
  byte gimbalZ;
};

MyData data;

void resetData() 
{
  data.throttle = 0;
  data.yaw = 127;
  data.pitch = 127;
  data.roll = 127;
  data.AUX1 = 0;
  data.AUX2 = 0;
  data.AUX3 = 0;
  data.AUX4 = 0;
  data.AUX5 = 0;
  data.AUX6 = 0;
  data.AUX7 = 0;
  data.gimbalY = 0;
  data.gimbalZ = 0;
}

void setup()
{
  //Start everything up
  pinMode(Pin_AUX1, INPUT_PULLUP);
  pinMode(Pin_AUX2, INPUT_PULLUP);
  pinMode(Pin_AUX3, INPUT_PULLUP);
  pinMode(Pin_AUX4, INPUT_PULLUP);
  pinMode(Pin_AUX5, INPUT_PULLUP);
  pinMode(Pin_AUX6, INPUT_PULLUP);
  pinMode(Pin_AUX7, INPUT_PULLUP);
  radio.begin();
  radio.setAutoAck(false);
  radio.setDataRate(RF24_250KBPS);
  radio.openWritingPipe(pipeOut);
  resetData();
}

int mapJoystickValues(int val, int lower, int middle, int upper, bool reverse)
{
  val = constrain(val, lower, upper);
  if ( val < middle )
    val = map(val, lower, middle, 0, 128);
  else
    val = map(val, middle, upper, 128, 255);
  return ( reverse ? 255 - val : val );
}

void loop()
{
  data.throttle = mapJoystickValues( analogRead(A0), 60, 490, 925, true );
  data.yaw      = mapJoystickValues( analogRead(A1),  0, 520, 956, false );
  data.pitch    = mapJoystickValues( analogRead(A2), 44, 502, 934, true );
  data.roll     = mapJoystickValues( analogRead(A3), 31, 320, 608, false );
  data.gimbalY  = map(analogRead(A6), 0, 1023, 0, 255);
  data.gimbalZ  = map(analogRead(A7), 0, 1023, 0, 255);
  data.AUX1     = digitalRead(Pin_AUX1);
  data.AUX2     = digitalRead(Pin_AUX2);
  data.AUX3     = digitalRead(Pin_AUX3);
  data.AUX4     = digitalRead(Pin_AUX4);
  data.AUX5     = digitalRead(Pin_AUX5);
  data.AUX6     = digitalRead(Pin_AUX6);
  data.AUX7     = digitalRead(Pin_AUX7);
  radio.write(&data, sizeof(MyData));
}

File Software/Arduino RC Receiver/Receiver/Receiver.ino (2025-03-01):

// RECEIVER

/*
 * This codes reads all of the channels from out transmitter and packs them into our PPM signal
 * For testing purposes, we can add Serial prints for all of the values to check if everything is working correctly
 * The roll on my transmitter is broken (bad potentiometer), so I've programmed the receiever to ignore that channel
 * unless a specific AUX is activated
 */

/* 
 *  This code is a modified version of the code from Electronoobs.com
 *  Check out his tutorial on the Arduino Drone
 */

#include <SPI.h>
#include <nRF24L01.h>
#include <RF24.h>

////////////////////// PPM CONFIGURATION//////////////////////////
#define channel_number 6  //set the number of channels
#define sigPin 2  //set PPM signal output pin on the arduino
#define PPM_FrLen 27000  //set the PPM frame length in microseconds (1ms = 1000µs)
#define PPM_PulseLen 400  //set the pulse length
//////////////////////////////////////////////////////////////////

int ppm[channel_number];

const uint64_t pipeIn =  0xE8E8F0F0E1LL;

RF24 radio(7, 8);

// The sizeof this struct should not exceed 32 bytes
struct MyData1 {
  byte throttle;
  byte yaw;
  byte pitch;
  byte roll;
  byte AUX1;
  byte AUX2;
  byte AUX3;
  byte AUX4;
  byte AUX5;
  byte AUX6;
  byte AUX7;
  byte gimbalY;
  byte gimbalZ;
};

MyData1 data;

void resetData() 
{
  // 'safe' values to use when no radio input is detected
  data.throttle = 0;
  data.yaw = 127;
  data.pitch = 127;
  data.roll = 127;
  data.AUX1 = 0;
  data.AUX2= 0;
  data.AUX3 = 0;
  data.AUX4 = 0;
  data.AUX5 = 0;
  data.AUX6 = 0;
  data.AUX7 = 0;
  data.gimbalY = 127;
  data.gimbalZ = 127;
  
  setPPMValuesFromData();
}

void setPPMValuesFromData()
{
  ppm[0] = map(data.throttle, 0, 255, 1000, 2000);
  ppm[1] = map(data.yaw, 0, 255, 1000, 2000);
  ppm[2] = map(data.pitch,    0, 255, 1000, 2000);

  
        
        if(data.AUX3 == 1){
          ppm[3] = 1500;
        }
        else{
          ppm[3] = map(data.roll,     0, 255, 1000, 2000);
        } 
      
  
  
  ppm[4] = map(data.AUX1,     0, 1, 1000, 2000);
  ppm[5] = map(data.AUX2,     0, 1, 1000, 2000);  
  }

/**************************************************/

void setupPPM() {
  pinMode(sigPin, OUTPUT);
  digitalWrite(sigPin, 0);  //set the PPM signal pin to the default state (off)

  cli();
  TCCR1A = 0; // set entire TCCR1 register to 0
  TCCR1B = 0;

  OCR1A = 100;  // compare match register (not very important, sets the timeout for the first interrupt)
  TCCR1B |= (1 << WGM12);  // turn on CTC mode
  TCCR1B |= (1 << CS11);  // 8 prescaler: 0,5 microseconds at 16mhz
  TIMSK1 |= (1 << OCIE1A); // enable timer compare interrupt
  sei();
}

void setup()
{  
  resetData();
  setupPPM();
  
  // Set up radio module
  radio.begin();
  radio.setDataRate(RF24_250KBPS); // Both endpoints must have this set the same
  radio.setAutoAck(false);

  radio.openReadingPipe(1,pipeIn);
  radio.startListening();
}

/**************************************************/

unsigned long lastRecvTime = 0;

void recvData()
{  
  while ( radio.available() ) {        
    radio.read(&data, sizeof(MyData1));
    lastRecvTime = millis();
  }
}

/**************************************************/

void loop()
{
  recvData();

  unsigned long now = millis();
  if ( now - lastRecvTime > 1000 ) {
    // signal lost?
    resetData();
  }
  
  setPPMValuesFromData();
}

/**************************************************/

//#error Delete this line befor you cahnge the value (clockMultiplier) below
#define clockMultiplier 2 // set this to 2 if you are using a 16MHz arduino, leave as 1 for an 8MHz arduino

ISR(TIMER1_COMPA_vect){
  static boolean state = true;

  TCNT1 = 0;

  if ( state ) {
    //end pulse
    PORTD = PORTD & ~B00000100; // turn pin 2 off. Could also use: digitalWrite(sigPin,0)
    OCR1A = PPM_PulseLen * clockMultiplier;
    state = false;
  }
  else {
    //start pulse
    static byte cur_chan_numb;
    static unsigned int calc_rest;

    PORTD = PORTD | B00000100; // turn pin 2 on. Could also use: digitalWrite(sigPin,1)
    state = true;

    if(cur_chan_numb >= channel_number) {
      cur_chan_numb = 0;
      calc_rest += PPM_PulseLen;
      OCR1A = (PPM_FrLen - calc_rest) * clockMultiplier;
      calc_rest = 0;
    }
    else {
      OCR1A = (ppm[cur_chan_numb] - PPM_PulseLen) * clockMultiplier;
      calc_rest += ppm[cur_chan_numb];
      cur_chan_numb++;
    }     
  }
}
